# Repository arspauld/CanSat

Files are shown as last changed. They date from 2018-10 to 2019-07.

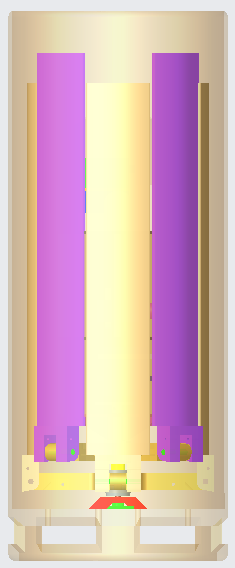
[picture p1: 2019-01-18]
mechanical/Screenshots from main folder/in container.PNG

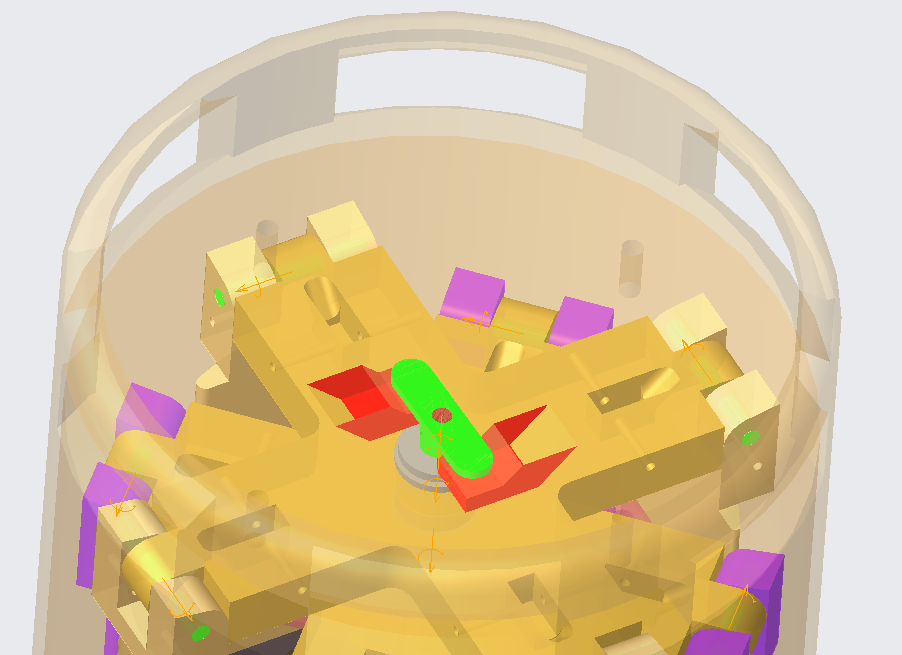
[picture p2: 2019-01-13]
mechanical/Screenshots from main folder/Release Mechanism Latched_2.PNG

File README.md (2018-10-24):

## Welcome to GitHub Pages

You can use the [editor on GitHub](https://github.com/arspauld/CanSat/edit/master/README.md) to maintain and preview the content for your website in Markdown files.

Whenever you commit to this repository, GitHub Pages will run [Jekyll](https://jekyllrb.com/) to rebuild the pages in your site, from the content in your Markdown files.

### Markdown

Markdown is a lightweight and easy-to-use syntax for styling your writing. It includes conventions for

```markdown
Syntax highlighted code block

# Header 1
## Header 2
### Header 3

- Bulleted
- List

1. Numbered
2. List

**Bold** and _Italic_ and `Code` text

[Link](url) and ![Image](src)
```

For more details see [GitHub Flavored Markdown](https://guides.github.com/features/mastering-markdown/).

### Jekyll Themes

Your Pages site will use the layout and styles from the Jekyll theme you have selected in your [repository settings](https://github.com/arspauld/CanSat/settings). The name of this theme is saved in the Jekyll `_config.yml` configuration file.

### Support or Contact

Having trouble with Pages? Check out our [documentation](https://help.github.com/categories/github-pages-basics/) or [contact support](https://github.com/contact) and we’ll help you sort it out.

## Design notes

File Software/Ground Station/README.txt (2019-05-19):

This is the folder for the files used on the ground station.
This will be done in Python programming

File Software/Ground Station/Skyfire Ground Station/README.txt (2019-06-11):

Skyfire Ground Station Setup:
	1. Insert XBee module into USB drive on laptop
	2. Open device manager and search for the port the XBee module is recognized as
	3. Open main.py and change the port in line <line #> to the exact name the XBee is recognized as in the device manager
	4. Open terminal
	5. Navigate to the Ground Station folder
	6. Run the file by typing "python main.py"

****There is a "frozen" instance of main.py that runs like an executable if the XBee is recognized as the same port as dictated by the program

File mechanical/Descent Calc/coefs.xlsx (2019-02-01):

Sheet: Cl and Cd
Alpha | Cl | Cd
-10 | -0.8195 | 0.07577
-9.75 | -0.8355 | 0.07025
-9.5 | -0.8519 | 0.06488
-9.25 | -0.8654 | 0.05977
-9 | -0.8743 | 0.055
-8.75 | -0.8723 | 0.05095
-8.5 | -0.8537 | 0.04867
-8.25 | -0.8499 | 0.04511
-8 | -0.8371 | 0.04218
-7.75 | -0.8225 | 0.03983
-7.5 | -0.8044 | 0.03756
-7.25 | -0.7876 | 0.0354
-7 | -0.7691 | 0.0335
-6.75 | -0.7491 | 0.03186
-6.5 | -0.7296 | 0.03038
-6.25 | -0.7105 | 0.02892
-6 | -0.6919 | 0.02765
-5.75 | -0.673 | 0.02658
-5.5 | -0.6548 | 0.02564
-5.25 | -0.6369 | 0.02482
-5 | -0.6195 | 0.02413
-4.75 | -0.6002 | 0.02367
-4.5 | -0.5816 | 0.02327
-4.25 | -0.5628 | 0.023
-4 | -0.5431 | 0.02285
-3.75 | -0.5227 | 0.02282
-3.5 | -0.503 | 0.02279
-3.25 | -0.4793 | 0.02298
-3 | -0.4493 | 0.02334
-2.75 | -0.4085 | 0.02382
-2.5 | -0.35 | 0.02437
-2.25 | -0.2694 | 0.02476
-2 | -0.1829 | 0.02464
-1.75 | -0.1037 | 0.02407
-1.5 | -0.0223 | 0.02312
-1.25 | 0.0255 | 0.0222
-1 | 0.0285 | 0.02168
-0.75 | 0.0275 | 0.02128
-0.5 | 0.0225 | 0.021
-0.25 | 0.0128 | 0.02083
0 | 0 | 0.02078
0.25 | -0.0128 | 0.02083
0.5 | -0.0225 | 0.02099
0.75 | -0.0275 | 0.02128
1 | -0.0285 | 0.02168
1.25 | -0.0255 | 0.02219
1.5 | 0.0223 | 0.02311
1.75 | 0.1036 | 0.02406
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

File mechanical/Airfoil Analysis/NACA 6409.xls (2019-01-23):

NACA 6409
1.00000 0.00094 | 0
0.99280 0.00313 | 0
0.97989 0.00699 | 0
0.96352 0.01177 | 0
0.94455 0.01717 | 0
0.92350 0.02296 | 0
0.90075 0.02900 | 0
0.87658 0.03516 | 0
0.85123 0.04135 | 0
0.82489 0.04749 | 0
0.79774 0.05350 | 0
0.76991 0.05932 | 0
0.74154 0.06492 | 0
0.71275 0.07024 | 0
0.68365 0.07525 | 0
0.65434 0.07992 | 0
0.62492 0.08422 | 0
0.59547 0.08814 | 0
0.56607 0.09165 | 0
0.53680 0.09474 | 0
0.50774 0.09740 | 0
0.47895 0.09963 | 0
0.45050 0.10141 | 0
0.42246 0.10275 | 0
0.39488 0.10365 | 0
0.36782 0.10391 | 0
0.34135 0.10345 | 0
0.31551 0.10230 | 0
0.29035 0.10049 | 0
0.26594 0.09807 | 0
0.24231 0.09508 | 0
0.21951 0.09156 | 0
0.19760 0.08756 | 0
0.17661 0.08315 | 0
0.15660 0.07836 | 0
0.13760 0.07326 | 0
0.11965 0.06790 | 0
0.10280 0.06235 | 0
0.08709 0.05666 | 0
0.07256 0.05088 | 0
0.05924 0.04509 | 0
0.04717 0.03932 | 0
0.03639 0.03364 | 0
0.02694 0.02810 | 0
0.01885 0.02274 | 0
0.01215 0.01760 | 0
0.00688 0.01273 | 0
0.00308 0.00816 | 0
0.00078 0.00391 | 0
0.00000 0.00000 | 0
0.00078 -0.00344 | 0
0.00308 -0.00632 | 0
0.00688 -0.00864 | 0
0.01215 -0.01043 | 0
0.01885 -0.01170 | 0
0.02694 -0.01248 | 0
0.03639 -0.01280 | 0
0.04717 -0.01269 | 0
0.05924 -0.01217 | 0
0.07256 -0.01130 | 0
0.08709 -0.01009 | 0
0.10280 -0.00859 | 0
0.11965 -0.00685 | 0
0.13760 -0.00490 | 0
0.15660 -0.00279 | 0
0.17661 -0.00057 | 0
0.19760 0.00171 | 0
0.21951 0.00401 | 0
0.24231 0.00627 | 0
0.26594 0.00845 | 0
0.29035 0.01049 | 0
0.31551 0.01235 | 0
0.34135 0.01397 | 0
0.36782 0.01531 | 0
0.39488 0.01633 | 0
0.42246 0.01708 | 0
0.45050 0.01774 | 0
0.47895 0.01830 | 0
0.50774 0.01873 | 0
0.53680 0.01902 | 0
0.56607 0.01916 | 0
0.59547 0.01913 | 0
0.62492 0.01892 | 0
0.65434 0.01852 | 0
0.68365 0.01793 | 0
0.71275 0.01716 | 0
0.74154 0.01620 | 0
0.76991 0.01507 | 0
0.79774 0.01377 | 0
0.82489 0.01234 | 0
0.85123 0.01078 | 0
0.87658 0.00913 | 0
0.90075 0.00742 | 0
0.92350 0.00569 | 0
0.94455 0.00399 | 0
0.96352 0.00238 | 0
0.97989 0.00092 | 0
0.99280 -0.00027 | 0
1.00000 -0.00094 | 0

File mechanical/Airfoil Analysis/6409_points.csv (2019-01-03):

x | y | z
1 | 0.00094 | 0
0.9928 | 0.00313 | 0
0.97989 | 0.00699 | 0
0.96352 | 0.01177 | 0
0.94455 | 0.01717 | 0
0.9235 | 0.02296 | 0
0.90075 | 0.029 | 0
0.87658 | 0.03516 | 0
0.85123 | 0.04135 | 0
0.82489 | 0.04749 | 0
0.79774 | 0.0535 | 0
0.76991 | 0.05932 | 0
0.74154 | 0.06492 | 0
0.71275 | 0.07024 | 0
0.68365 | 0.07525 | 0
0.65434 | 0.07992 | 0
0.62492 | 0.08422 | 0
0.59547 | 0.08814 | 0
0.56607 | 0.09165 | 0
0.5368 | 0.09474 | 0
0.50774 | 0.0974 | 0
0.47895 | 0.09963 | 0
0.4505 | 0.10141 | 0
0.42246 | 0.10275 | 0
0.39488 | 0.10365 | 0
0.36782 | 0.10391 | 0
0.34135 | 0.10345 | 0
0.31551 | 0.1023 | 0
0.29035 | 0.10049 | 0
0.26594 | 0.09807 | 0
0.24231 | 0.09508 | 0
0.21951 | 0.09156 | 0
0.1976 | 0.08756 | 0
0.17661 | 0.08315 | 0
0.1566 | 0.07836 | 0
0.1376 | 0.07326 | 0
0.11965 | 0.0679 | 0
0.1028 | 0.06235 | 0
0.08709 | 0.05666 | 0
0.07256 | 0.05088 | 0
0.05924 | 0.04509 | 0
0.04717 | 0.03932 | 0
0.03639 | 0.03364 | 0
0.02694 | 0.0281 | 0
0.01885 | 0.02274 | 0
0.01215 | 0.0176 | 0
0.00688 | 0.01273 | 0
0.00308 | 0.00816 | 0
0.00078 | 0.00391 | 0
0 | 0 | 0
0.00078 | -0.00344 | 0
0.00308 | -0.00632 | 0
0.00688 | -0.00864 | 0
0.01215 | -0.01043 | 0
0.01885 | -0.0117 | 0
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

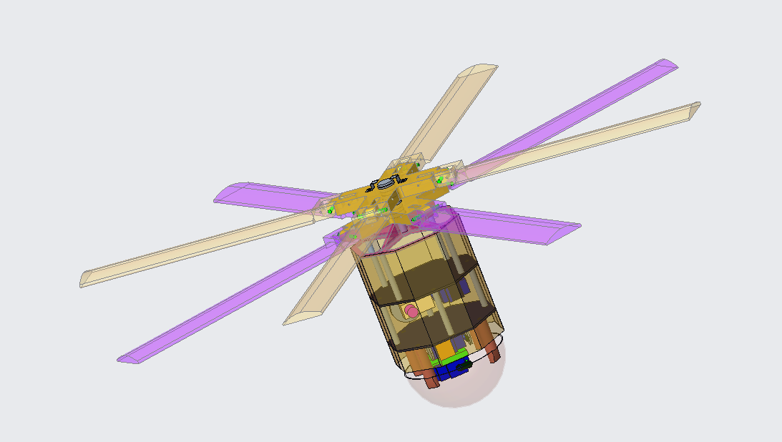
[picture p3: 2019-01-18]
mechanical/Screenshots from main folder/iso view.PNG

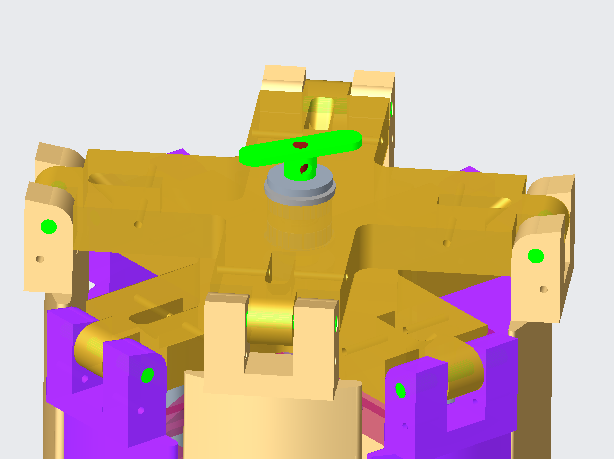
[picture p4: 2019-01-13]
mechanical/Screenshots from main folder/Top Release Mechanism.PNG

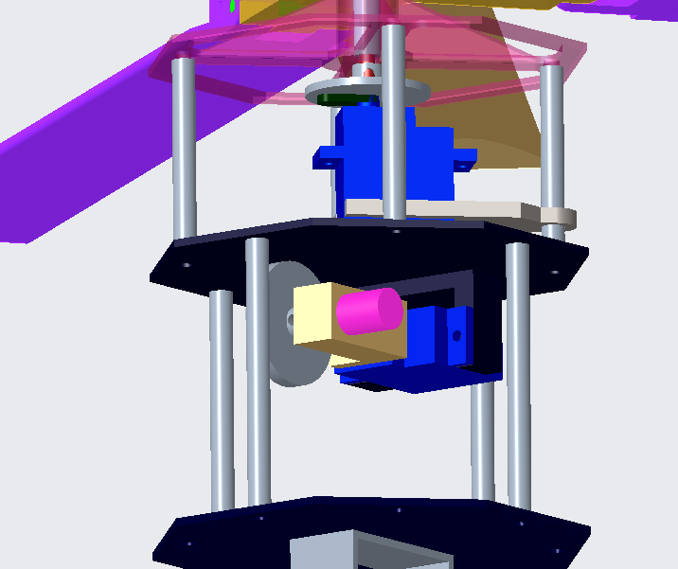
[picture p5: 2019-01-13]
mechanical/Screenshots from main folder/Control Moment Gyro 4.PNG

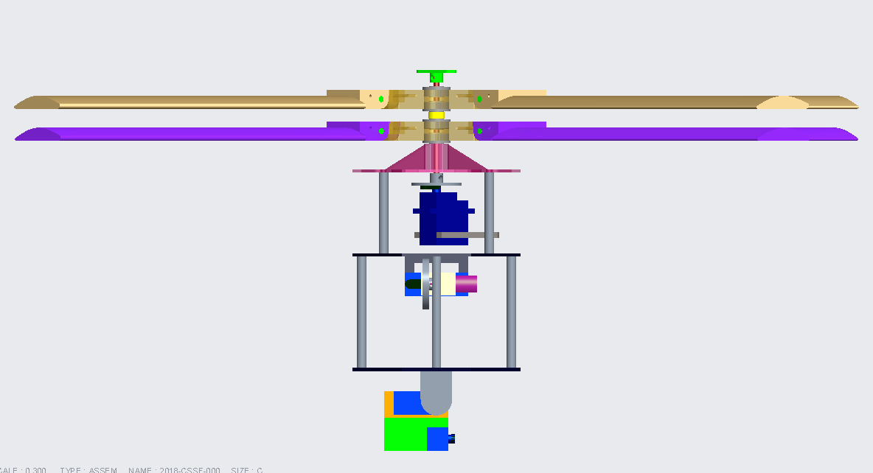
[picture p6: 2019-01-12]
mechanical/Screenshots from main folder/Full deployed Drawing.PNG

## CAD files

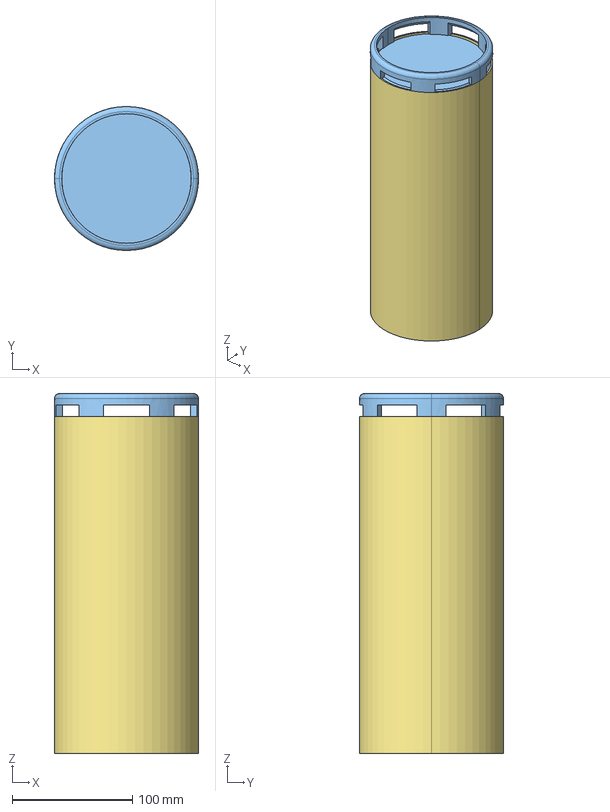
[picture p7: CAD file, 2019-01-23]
mechanical/2018-cssf-000_asm.stp
120.0 x 120.0 x 300.0 mm
2018-CSSF-101
2018-CSSF-102 x 4
2018-CSSF-103
2018-CSSF-106 x 4
2018-CSSF-105
MICRO_SERVO x 4
SERVO_ARM x 3
2018-CSSF-502
GYRO_MOTOR
2018-CSSF-501
2018-CSSF-201
2018-CSSF-202
2018-CSSF-203
2018-CSSF-301
57155K337_STAINLESS_STEEL_BALL_ x 6
2018-CSSF-303_TOP
2018-CSSF-302
2018-CSSF-303
ROTOR1_WING x 4
2018-CSSF-306 x 12
ROTOR2_WING x 4
2018-CSSF-301B
2018-CSSF-307B
2018-CSSF-305B x 4
2018-CSSF-307 x 2
CONTAINER
CAMERA_DOME
6409_NACA_ROTOR
DOME_OFFSET x 4
CANSAT_SHELL x 2
CONTAINER_SLEEVE_1
SERVO_ARM_FULL_LENGTH
RELEASE_CATCH x 2
PAYLOAD_DOWEL x 2

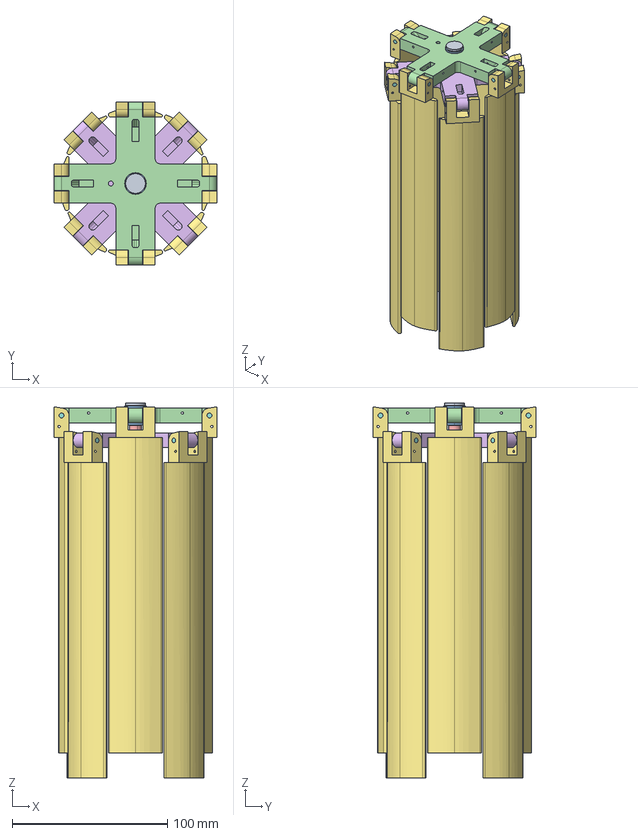
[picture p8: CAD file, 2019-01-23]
mechanical/SolidEdge/Original Creo Parts/2018-cssf-300_asm.stp
104.8 x 104.8 x 241.5 mm
2018-CSSF-301
57155K337_STAINLESS_STEEL_BALL_ x 4
2018-CSSF-303_TOP
2018-CSSF-302
2018-CSSF-303
ROTOR1_WING x 4
2018-CSSF-306 x 8
ROTOR2_WING x 4

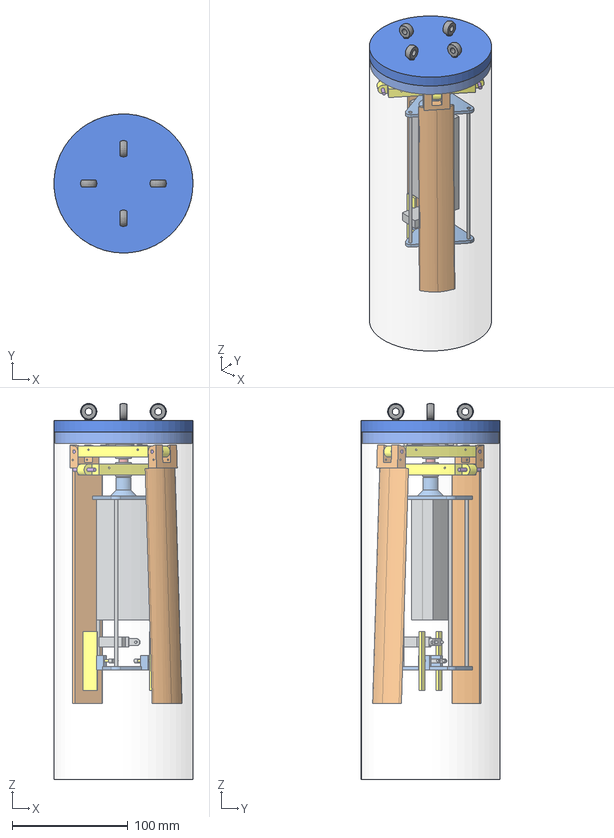
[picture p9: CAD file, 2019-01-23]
mechanical/SolidEdge/Container Parts/Container Assembly_v3.stp
120.0 x 120.0 x 324.5 mm
Container Top
Container Shell
Wooden Dowel M3 x 2
M6 EyeBolt x 4
m3_all_thread x 3
hardware_plate
FIN_LEVER x 2
BALL_PIN x 4
FIN x 2
NANO_SERVO_HS-40
SERVO_ARM
HARDWARE_BOTTOM_PLATE_V2
2018-CSSF-301
57155K337_STAINLESS_STEEL_BALL_ x 4
2018-CSSF-303_TOP
2018-CSSF-302
2018-CSSF-303
ROTOR1_WING x 2
ROTOR2_WING x 2
2018-CSSF-306 x 4
Lip1 x 2
3.2mm screw x 3
PCB_CASE_BACK
PCB
PCB_CASE_FRONT

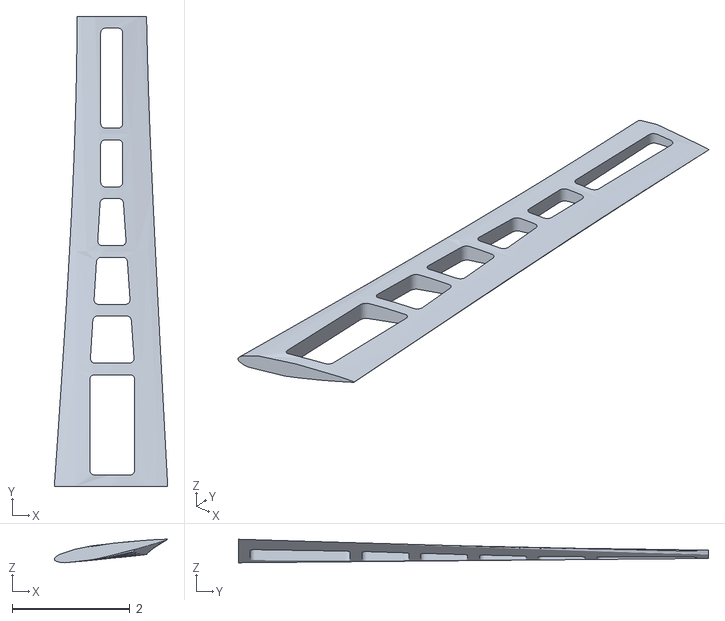
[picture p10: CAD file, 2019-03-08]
mechanical/AIRFOIL X-SECTIONS/20cm_0012_rotor_lh.stl
1.93 x 7.99 x 0.401

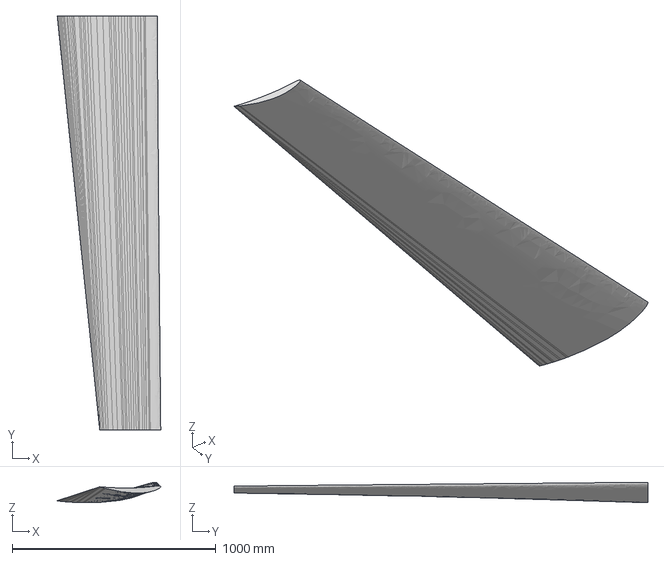
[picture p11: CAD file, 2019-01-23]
mechanical/Naca/6409_blade.step
507.9 x 2030.0 x 100.4 mm

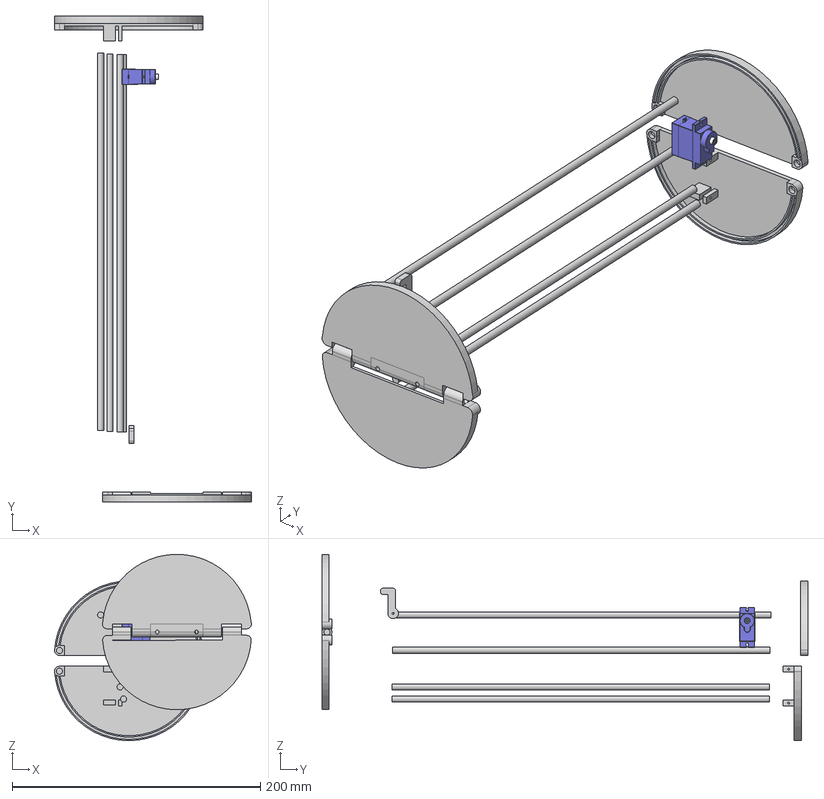
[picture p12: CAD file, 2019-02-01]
mechanical/SolidEdge/2nd Container Design/Container 2 parts.step
158.7 x 391.4 x 150.1 mm
Outer Top
Top 1
Rod x 4
Bottom empty half
Bottom servo half
servo

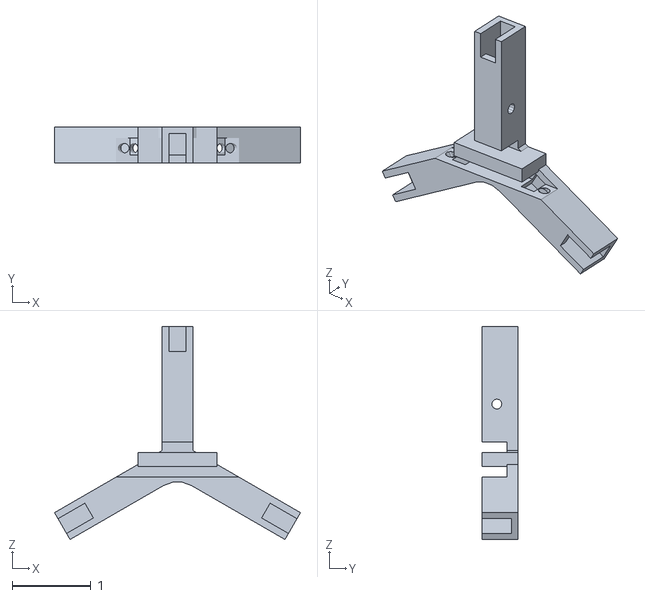
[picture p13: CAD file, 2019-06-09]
mechanical/SolidEdge/3 Blade/LANDING_GEAR_MOUNT.stl
3.12 x 0.453 x 2.70

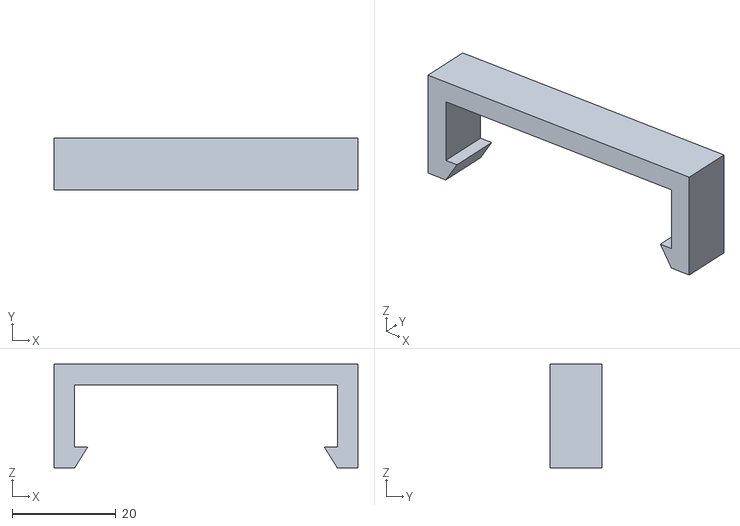
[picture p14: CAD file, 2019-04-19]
mechanical/SolidEdge/Battery Parts/BATTERY_LOCK.stl
58.7 x 10.0 x 20.0

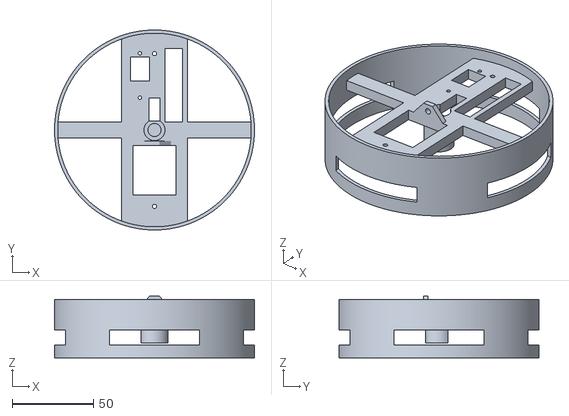
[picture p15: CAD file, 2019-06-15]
mechanical/SolidEdge/Container Parts/Container Top V4.stl
123.0 x 123.0 x 38.0

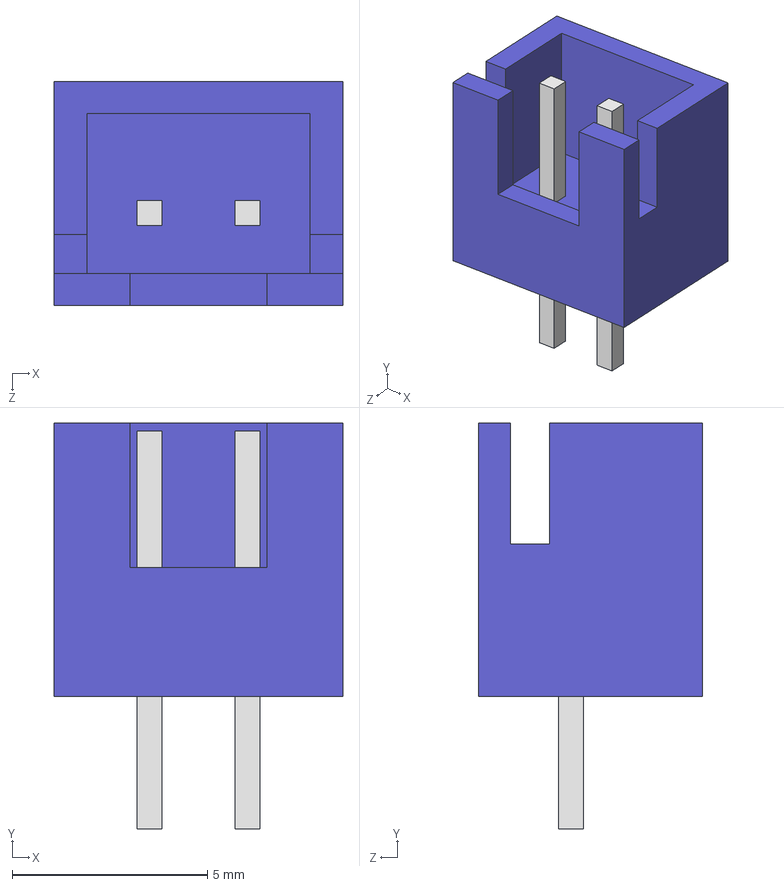
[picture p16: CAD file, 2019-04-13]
mechanical/SolidEdge/Electronics Parts/B2B-XH-A.IGS
7.40 x 10.4 x 5.75 mm

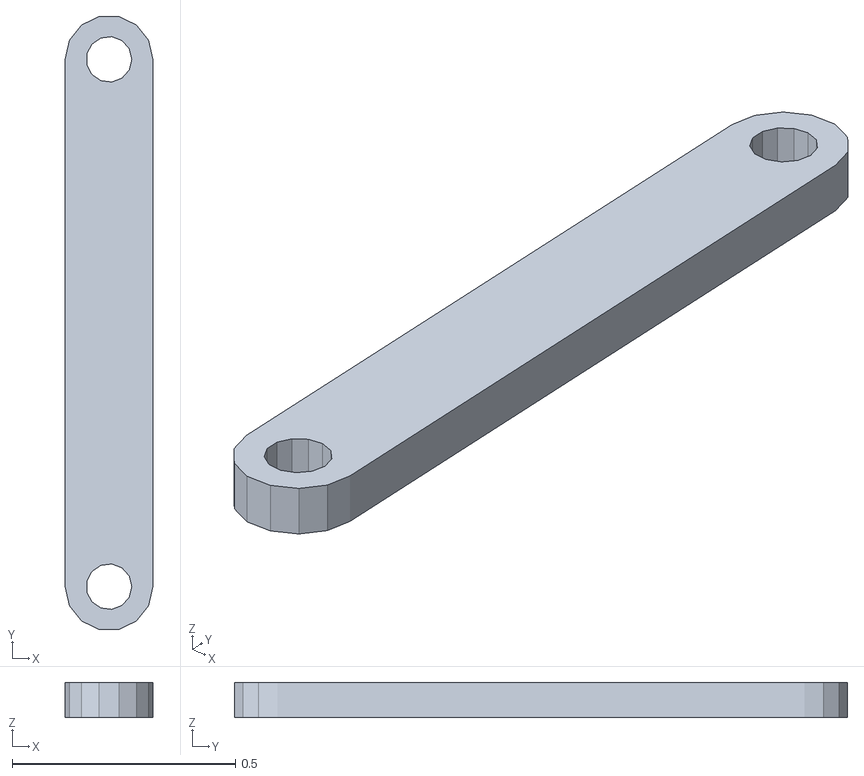
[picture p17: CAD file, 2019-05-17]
mechanical/SolidEdge/Fin Designs/control_arm.stl
0.197 x 1.37 x 0.0787

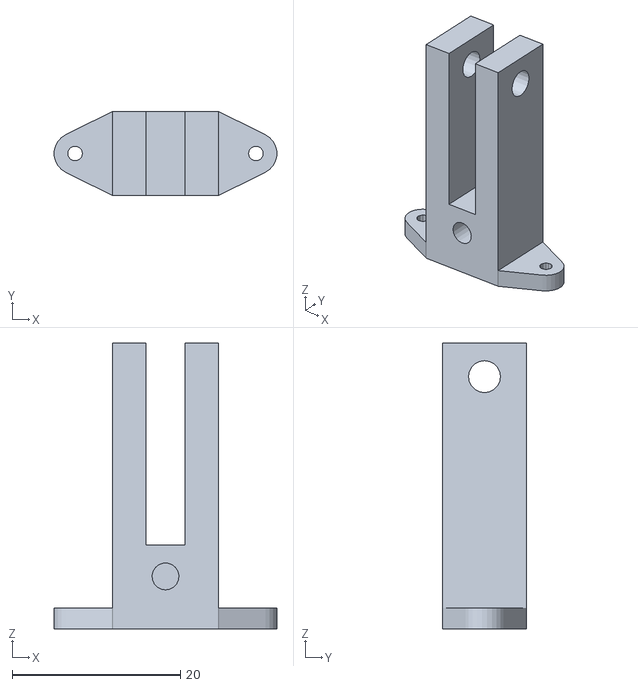
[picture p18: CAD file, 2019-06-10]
mechanical/SolidEdge/Fin Designs/Fin Redesign/FinR_connector_V1.stl
26.5 x 10.0 x 34.0

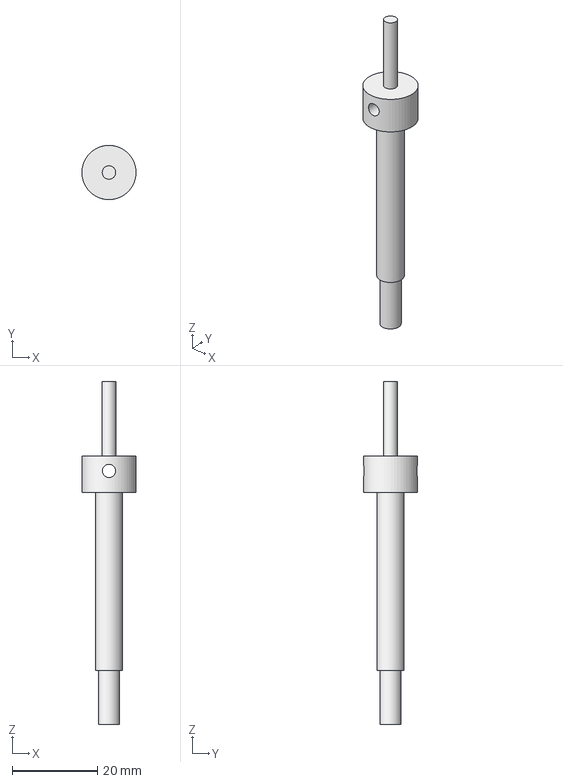
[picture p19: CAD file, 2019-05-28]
mechanical/SolidEdge/Original Creo Parts/2018-CSSF-301.stp
12.7 x 12.7 x 80.3 mm

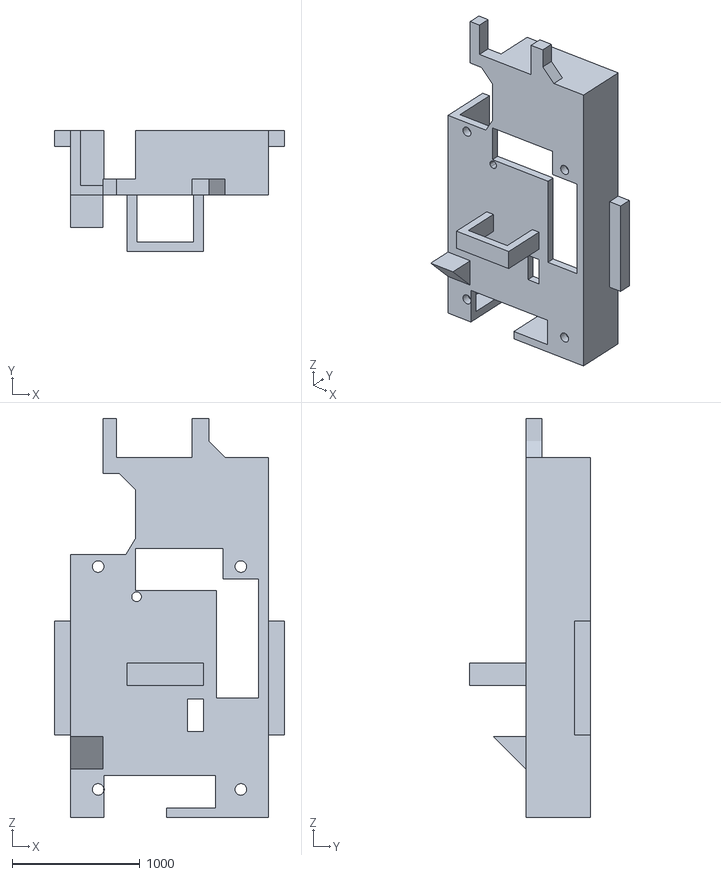
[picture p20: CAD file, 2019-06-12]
mechanical/SolidEdge/PCB Cases/PCB_CASE_V5_FRONT.stl
1803.4 x 950.6 x 3124.2

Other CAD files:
mechanical/SolidEdge/RELEASE_ARM.stl
mechanical/SolidEdge/Rotor Parts/hub_adapter_signboard v1.stl
mechanical/SolidEdge/U-Frame/U-frame_top_draft_model.stp
mechanical/AIRFOIL X-SECTIONS/20cm_0012_rotor.stl
mechanical/AIRFOIL X-SECTIONS/20cm_0012_rotor_xsect_1.stl
mechanical/AIRFOIL X-SECTIONS/20cm_0012_rotor_xsect_1_mirror.stl
mechanical/AIRFOIL X-SECTIONS/20cm_0012_rotor_xsect_2.stl
mechanical/AIRFOIL X-SECTIONS/20cm_0012_rotor_xsect_2_mirror.stl
mechanical/AIRFOIL X-SECTIONS/20cm_0012_rotor_xsect_3.stl
mechanical/AIRFOIL X-SECTIONS/20cm_0012_rotor_xsect_3_mirror.stl
mechanical/AIRFOIL X-SECTIONS/20cm_0012_rotor_xsect_4.stl
mechanical/AIRFOIL X-SECTIONS/20cm_0012_rotor_xsect_4_mirror.stl
mechanical/AIRFOIL X-SECTIONS/20cm_0012_rotor_xsect_5.stl
mechanical/AIRFOIL X-SECTIONS/20cm_0012_rotor_xsect_5_mirror.stl
mechanical/AIRFOIL X-SECTIONS/20cm_0012_rotor_xsect_6.stl
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

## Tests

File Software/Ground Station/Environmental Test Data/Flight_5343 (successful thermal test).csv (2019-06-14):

Team ID | Mission Time | Packet Count | Altitude | Pressure | Temperature | Voltage | GPS Time | GPS Latitude | GPS Longitude | GPS Altitude | GPS Sats | Pitch | Roll | Blade Spin Rate | Flight State | Bonus Direction
5343 | 1 | 1 | 0.1 | 96969 | 47.8 | 5.6 | 16:12:16 | 0 | 0 | 0 | 0 | 0 | 0 | 0 | 0 | 154
5343 | 2 | 2 | 0.2 | 96970 | 47.9 | 5.6 | 16:12:17 | 0 | 0 | 0 | 0 | 0 | 0 | 0 | 0 | 154
5343 | 3 | 3 | 0.1 | 96969 | 47.8 | 5.6 | 16:12:18 | 0 | 0 | 0 | 0 | 0 | 0 | 0 | 0 | 154
5343 | 4 | 4 | 0.2 | 96970 | 47.8 | 5.6 | 16:12:19 | 0 | 0 | 0 | 0 | 0 | 0 | 0 | 0 | 154
5343 | 5 | 5 | 0.3 | 96971 | 47.8 | 5.6 | 16:12:20 | 0 | 0 | 0 | 0 | 0 | 0 | 0 | 0 | 154
5343 | 6 | 6 | 0.5 | 96973 | 47.8 | 5.6 | 16:12:21 | 0 | 0 | 0 | 0 | 0 | 0 | 0 | 0 | 154
5343 | 7 | 7 | 0.5 | 96973 | 47.8 | 5.6 | 16:12:22 | 0 | 0 | 0 | 0 | 0 | 0 | 0 | 0 | 154
5343 | 8 | 8 | 0.3 | 96971 | 47.8 | 5.6 | 16:12:23 | 0 | 0 | 0 | 0 | 0 | 0 | 0 | 0 | 154
5343 | 9 | 9 | 0.5 | 96973 | 47.9 | 5.5 | 16:12:24 | 0 | 0 | 0 | 0 | 0 | 0 | 0 | 0 | 154
5343 | 10 | 10 | 0.7 | 96975 | 48 | 5.6 | 16:12:25 | 0 | 0 | 0 | 0 | 0 | 0 | 0 | 0 | 154
5343 | 11 | 11 | 0.6 | 96974 | 48.1 | 5.6 | 16:12:26 | 0 | 0 | 0 | 0 | 0 | 0 | 0 | 0 | 154
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

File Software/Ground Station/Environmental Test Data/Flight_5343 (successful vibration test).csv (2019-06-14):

Team ID | Mission Time | Packet Count | Altitude | Pressure | Temperature | Voltage | GPS Time | GPS Latitude | GPS Longitude | GPS Altitude | GPS Sats | Pitch | Roll | Blade Spin Rate | Flight State | Bonus Direction
5343 | 351 | 351 | -1.7 | 97111 | 32.5 | 5.4 | 04:47:06 | 0.0 | 0.0 | 0.0 | 0 | -6 | -5 | 0 | 0 | 35
5343 | 352 | 352 | -1.8 | 97112 | 32.5 | 5.4 | 04:47:07 | 0.0 | 0.0 | 0.0 | 0 | 1 | 2 | 0 | 0 | 35
5343 | 353 | 353 | -1.7 | 97111 | 32.5 | 5.5 | 04:47:08 | 0.0 | 0.0 | 0.0 | 0 | 1 | 2 | 0 | 0 | 35
5343 | 354 | 354 | -1.7 | 97111 | 32.5 | 5.4 | 04:47:09 | 0.0 | 0.0 | 0.0 | 0 | 1 | 2 | 0 | 0 | 35
5343 | 355 | 355 | -1.7 | 97111 | 32.5 | 5.4 | 04:47:10 | 0.0 | 0.0 | 0.0 | 0 | 1 | 2 | 0 | 0 | 35
5343 | 1 | 1 | 0.0 | 97112 | 32.5 | 5.4 | 04:47:15 | 0.0 | 0.0 | 0.0 | 0 | 0 | -7 | 0 | 0 | 35
5343 | 2 | 2 | 0.1 | 97114 | 32.5 | 5.4 | 04:47:15 | 0.0 | 0.0 | 0.0 | 0 | 0 | 0 | 0 | 0 | 35
5343 | 3 | 3 | 0.0 | 97113 | 32.4 | 4.5 | 04:47:16 | 0.0 | 0.0 | 0.0 | 0 | 0 | 0 | 0 | 0 | 35
5343 | 4 | 4 | 0.1 | 97113 | 32.5 | 5.4 | 04:47:17 | 0.0 | 0.0 | 0.0 | 0 | 0 | 0 | 0 | 0 | 35
5343 | 5 | 5 | 0.1 | 97113 | 32.4 | 5.4 | 04:47:18 | 0.0 | 0.0 | 0.0 | 0 | 0 | 0 | 0 | 0 | 35
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

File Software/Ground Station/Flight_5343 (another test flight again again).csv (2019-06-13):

Team ID | Mission Time | Packet Count | Altitude | Pressure | Temperature | Voltage | GPS Time | GPS Latitude | GPS Longitude | GPS Altitude | GPS Sats | Pitch | Roll | Blade Spin Rate | Flight State | Bonus Direction
5343 | 1 | 1 | 0 | 98635 | 23.5 | 2.7 | 00:00:00 | 0.0 | 0.0 | 0.0 | 0 | 0 | 0 | 30 | 0 | 0
5343 | 2 | 2 | 0 | 98637 | 23.4 | 2.6 | 00:00:00 | 0.0 | 0.0 | 0.0 | 0 | 0 | 0 | 15 | 0 | 0
5343 | 3 | 3 | 0 | 98636 | 23.0 | 2.6 | 00:00:00 | 0.0 | 0.0 | 0.0 | 0 | 0 | 0 | 7 | 0 | 0
5343 | 4 | 4 | 0 | 98637 | 23.0 | 2.6 | 00:00:00 | 0.0 | 0.0 | 0.0 | 0 | 0 | 0 | 3 | 0 | 0
5343 | 5 | 5 | 0 | 98635 | 22.9 | 2.6 | 00:00:00 | 0.0 | 0.0 | 0.0 | 0 | 0 | 0 | 1 | 0 | 0
5343 | 6 | 6 | 0 | 98635 | 25.2 | 2.8 | 00:00:00 | 0.0 | 0.0 | 0.0 | 0 | 0 | 0 | 2580 | 0 | 0
5343 | 7 | 7 | 0 | 98634 | 25.2 | 2.8 | 00:00:00 | 0.0 | 0.0 | 0.0 | 0 | 0 | 0 | 1350 | 0 | 0
5343 | 8 | 8 | 0 | 98638 | 25.5 | 2.8 | 00:00:00 | 0.0 | 0.0 | 0.0 | 0 | 0 | 0 | 945 | 0 | 0
5343 | 9 | 9 | 0 | 98636 | 25.3 | 2.8 | 00:00:00 | 0.0 | 0.0 | 0.0 | 0 | 0 | 0 | 682 | 0 | 0
5343 | 10 | 10 | 0 | 98637 | 25.4 | 2.8 | 00:00:00 | 0.0 | 0.0 | 0.0 | 0 | 0 | 0 | 341 | 0 | 0
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

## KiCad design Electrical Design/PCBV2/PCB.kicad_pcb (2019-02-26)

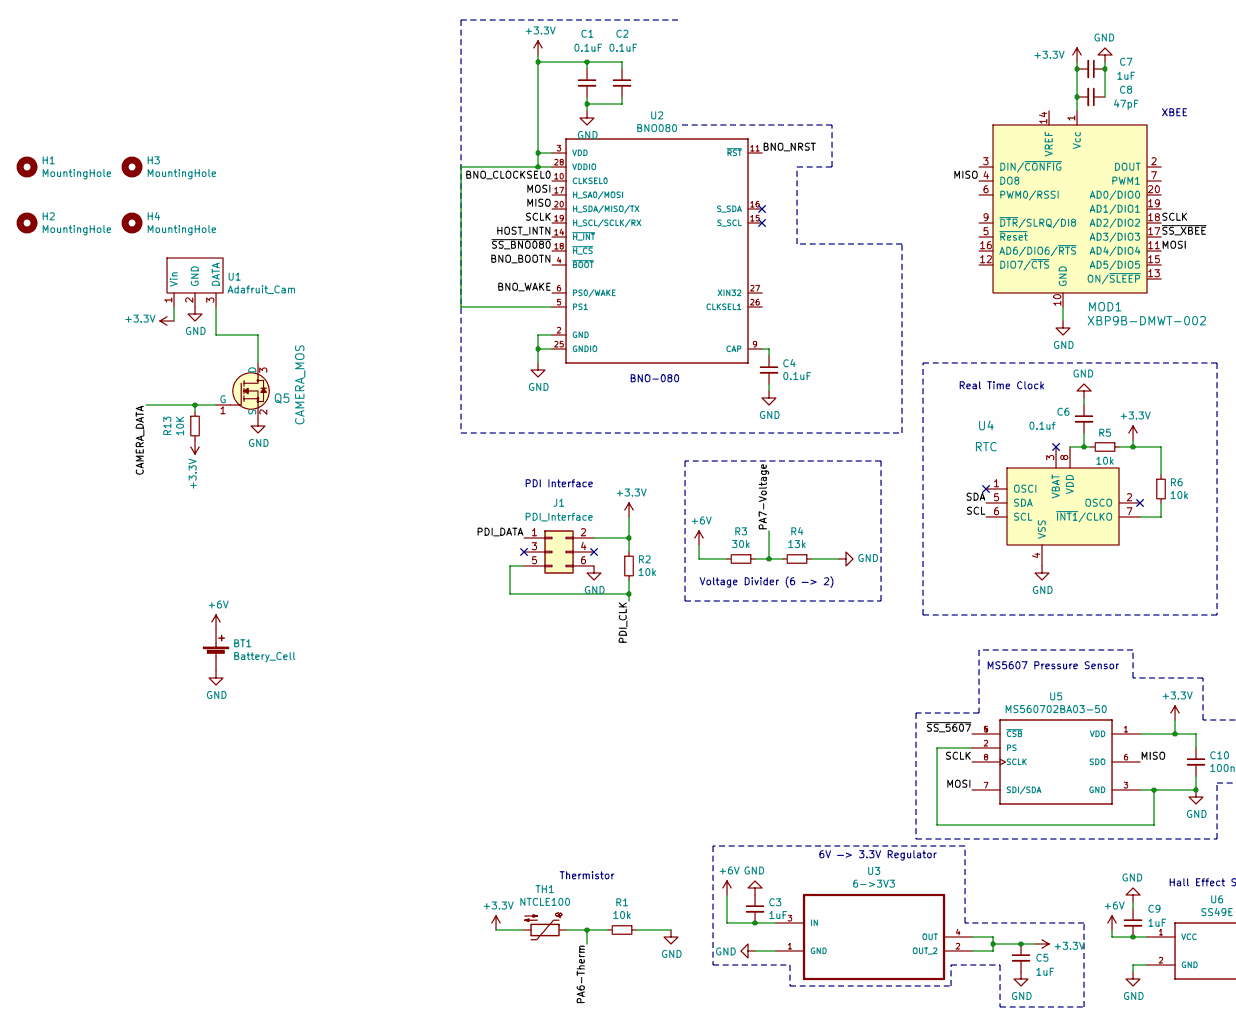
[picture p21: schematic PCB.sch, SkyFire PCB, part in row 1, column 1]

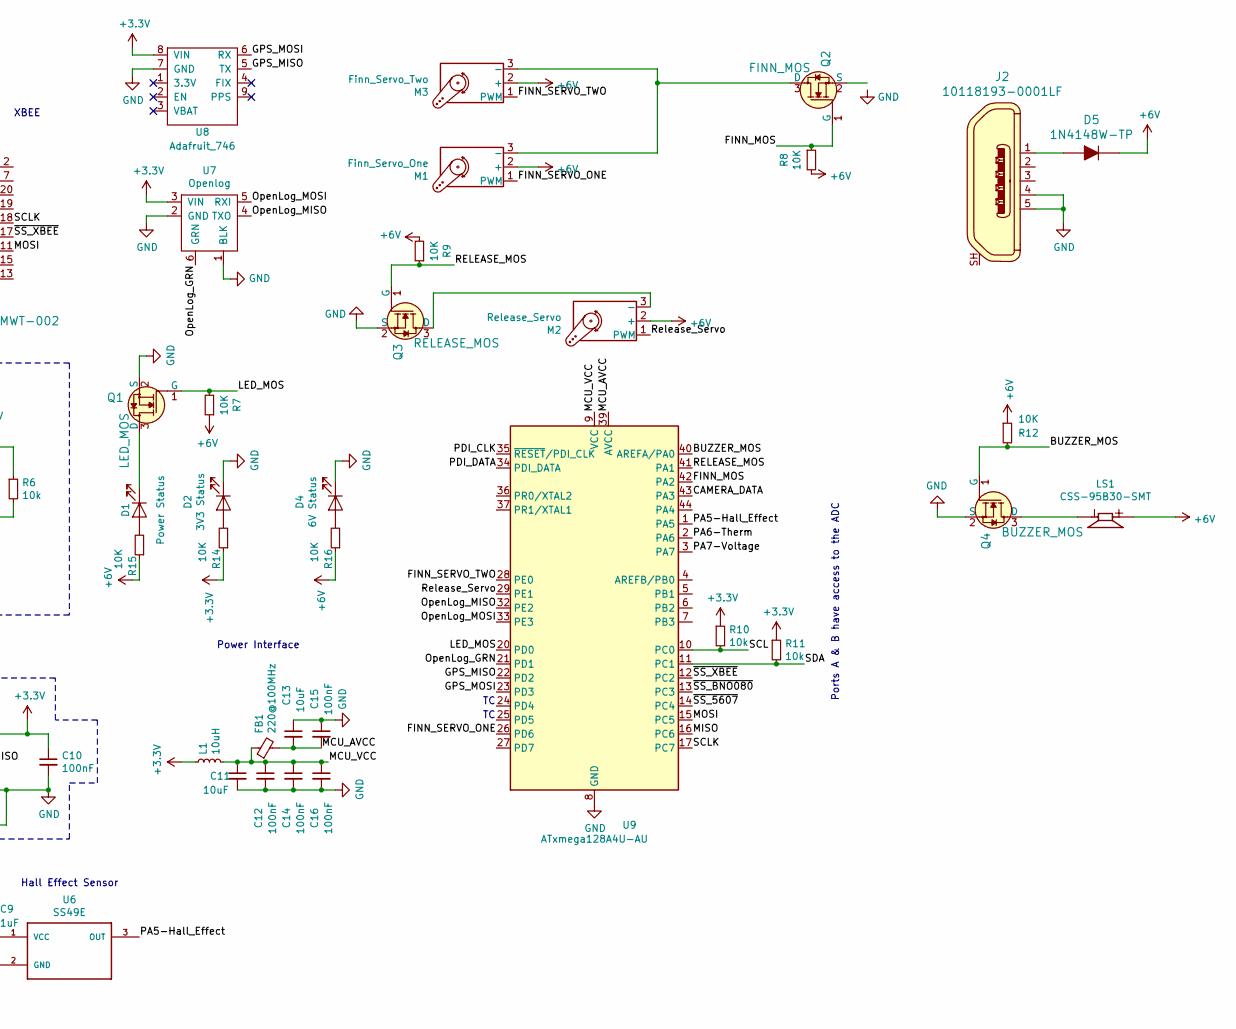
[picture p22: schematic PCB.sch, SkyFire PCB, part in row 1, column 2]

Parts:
BT1: Battery_Cell; MOLEX-1X2_LOCK
C1, C2, C4: 0.1uF; C_0805_2012Metric_Pad1.15x1.40mm_HandSolder
C3, C5, C7, C9: 1uF; C_0805_2012Metric_Pad1.15x1.40mm_HandSolder
C6: 0.1uf; C_0805_2012Metric_Pad1.15x1.40mm_HandSolder
C8: 47pF; C_0805_2012Metric_Pad1.15x1.40mm_HandSolder
C10, C12, C14, C15, C16: 100nF; C_0805_2012Metric_Pad1.15x1.40mm_HandSolder
C11, C13: 10uF; C_0805_2012Metric_Pad1.15x1.40mm_HandSolder
D1: Power Status; LED_0603_1608Metric_Pad1.05x0.95mm_HandSolder
D2: 3V3 Status; LED_0603_1608Metric_Pad1.05x0.95mm_HandSolder
D4: 6V Status; LED_0603_1608Metric_Pad1.05x0.95mm_HandSolder
D5: 1N4148W-TP; SOD-123; MPN 1N4148W-TP; Digi-Key_PN 1N4148WTPMSCT-ND
FB1: 220@100MHz; L_0805_2012Metric_Pad1.15x1.40mm_HandSolder
H1, H2, H3, H4: MountingHole; MountingHole_3.2mm_M3
J1: PDI_Interface; 2X3
J2: 10118193-0001LF; USB_Micro_B_Female_10118193-0001LF; MPN 10118193-0001LF; Digi-Key_PN 609-4616-1-ND
L1: 10uH; L_0805_2012Metric_Pad1.15x1.40mm_HandSolder
LS1: CSS-95B30-SMT; CUI_CSS-95B30-SMT
M1: Finn_Servo_One; MOLEX-1X3_LOCK
M2: Release_Servo; MOLEX-1X3_LOCK
M3: Finn_Servo_Two; MOLEX-1X3_LOCK
MOD1: XBP9B-DMWT-002; XBEE_PRO-20_THT; MPN XBP9B-DMWT-002; Digi-Key_PN 602-1301-ND
Q1: LED_MOS; SOT-23-3; MPN 2N7002K-T1-E3; Digi-Key_PN 2N7002K-T1-E3CT-ND
Q2: FINN_MOS; SOT-23-3; MPN 2N7002K-T1-E3; Digi-Key_PN 2N7002K-T1-E3CT-ND
Q3: RELEASE_MOS; SOT-23-3; MPN 2N7002K-T1-E3; Digi-Key_PN 2N7002K-T1-E3CT-ND
Q4: BUZZER_MOS; SOT-23-3; MPN 2N7002K-T1-E3; Digi-Key_PN 2N7002K-T1-E3CT-ND
Q5: CAMERA_MOS; SOT-23-3; MPN 2N7002K-T1-E3; Digi-Key_PN 2N7002K-T1-E3CT-ND
R1, R2, R5, R6, R10, R11: 10k; R_0805_2012Metric_Pad1.15x1.40mm_HandSolder
R3: 30k; R_0805_2012Metric_Pad1.15x1.40mm_HandSolder
R4: 13k; R_0805_2012Metric_Pad1.15x1.40mm_HandSolder
R7, R8, R9, R12, R13, R14, R15, R16: 10K; R_0805_2012Metric_Pad1.15x1.40mm_HandSolder
TH1: NTCLE100; CP_Radial_D4.0mm_P1.50mm
U1: Adafruit_Cam; MOLEX-1X3_LOCK
U2: BNO080; LGA-28
U3: 6->3V3; SOT230P700X180-4N
U4: RTC; SOIC-8_W3.9mm; MPN PCF8523T/1,118; Digi-Key_PN 568-5306-1-ND
U5: MS560702BA03-50; SON125P300X500X100-8N
U6: SS49E; MOLEX-1X3_LOCK
U7: Openlog; 1X06
U8: Adafruit_746; 1X09
U9: ATxmega128A4U-AU; TQFP-44_10x10mm_P0.8mm

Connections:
+3V3: C1.1, C2.1, C5.1, C7.2, C8.2, C10.1, J1.2, L1.1, MOD1.1 (Vcc), R2.1, R5.1, R6.1, R10.1, R11.1, R13.2, R14.1, TH1.2, U1.1 (Vin), U2.3 (VDD), U2.5 (PS1), U2.28 (VDDIO), U3.2 (OUT_2), U3.4 (OUT), U5.1 (VDD), U7.3 (VIN), U8.8 (VIN)
+6V: BT1.1 (+), C3.2, C9.2, D5.K, LS1.P, M1.2 (+), M2.2 (+), M3.2 (+), R3.2, R7.1, R8.2, R9.2, R12.1, R15.1, R16.1, U3.3 (IN), U6.1 (VCC)
/BNO_BOOTN: U2.4 (~BOOT~)
/BNO_CLOCKSEL0: U2.10 (CLKSEL0)
/BNO_NRST: U2.11 (~RST~)
/BNO_WAKE: U2.6 (PS0/WAKE)
/BUZZER_MOS: Q4.1 (G), R12.2, U9.40 (AREFA/PA0)
/CAMERA_DATA: Q5.1 (G), R13.1, U9.43 (PA3)
/FINN_MOS: Q2.1 (G), R8.1, U9.42 (PA2)
/FINN_SERVO_ONE: M1.1 (PWM), U9.26 (PD6)
/FINN_SERVO_TWO: M3.1 (PWM), U9.28 (PE0)
/GPS_MISO: U8.5 (TX), U9.22 (PD2)
/GPS_MOSI: U8.6 (RX), U9.23 (PD3)
/HOST_INTN: U2.14 (~H_INT~)
/LED_MOS: Q1.1 (G), R7.2, U9.20 (PD0)
/MCU_AVCC: C13.2, C15.2, FB1.2, U9.39 (AVCC)
/MCU_VCC: C11.1, C12.1, C14.1, C16.1, FB1.1, L1.2, U9.9 (VCC), U9.19 (VCC), U9.31 (VCC)
/MISO: MOD1.4 (DO8), U2.20 (H_SDA/MISO/TX), U5.6 (SDO), U9.16 (PC6)
/MOSI: MOD1.11 (AD4/DIO4), U2.17 (H_SA0/MOSI), U5.7 (SDI/SDA), U9.15 (PC5)
/OpenLog_GRN: U7.6 (GRN), U9.21 (PD1)
/OpenLog_MISO: U7.4 (TXO), U9.32 (PE2)
/OpenLog_MOSI: U7.5 (RXI), U9.33 (PE3)
/PA5-Hall_Effect: U6.3 (OUT), U9.1 (PA5)
/PA6-Therm: R1.2, TH1.1, U9.2 (PA6)
/PA7-Voltage: R3.1, R4.2, U9.3 (PA7)
/PDI_CLK: J1.5, R2.2, U9.35 (~RESET~/PDI_CLK)
/PDI_DATA: J1.1, U9.34 (PDI_DATA)
/RELEASE_MOS: Q3.1 (G), R9.1, U9.41 (PA1)
/Release_Servo: M2.1 (PWM), U9.29 (PE1)
/SCL: R10.2, U4.6 (SCL), U9.10 (PC0)
/SCLK: MOD1.18 (AD2/DIO2), U2.19 (H_SCL/SCLK/RX), U5.8 (SCLK), U9.17 (PC7)
/SDA: R11.2, U4.5 (SDA), U9.11 (PC1)
/~SS_5607: U5.4 (~CSB~), U5.5 (~CSB~), U9.14 (PC4)
/~SS_BNO080: U2.18 (~H_CS~), U9.13 (PC3)
/~SS_XBEE: MOD1.17 (AD3/DIO3), U9.12 (PC2)
GND: BT1.2 (-), C1.2, C2.2, C3.1, C4.2, C5.2, C6.1, C7.1, C8.1, C9.1, C10.2, C11.2, C12.2, C13.1, C14.2, C15.1, C16.2, D2.1 (K), D4.1 (K), J1.6, J2.4, J2.5, MOD1.10 (GND), Q1.2 (S), Q3.2 (S), Q4.2 (S), Q5.2 (S), R1.1, R4.1, U1.2 (GND), U2.2 (GND), U2.25 (GNDIO), U3.1 (GND), U4.4 (VSS), U5.2 (PS), U5.3 (GND), U6.2 (GND), U7.1 (BLK), U7.2 (GND), U8.7 (GND), U9.8 (GND), U9.18 (GND), U9.30 (GND), U9.38 (GND)
unnamed: C4.1, U2.9 (CAP)
unnamed: C6.2, R5.2, U4.8 (VDD)
unnamed: D1.1 (K), Q1.3 (D)
unnamed: D1.2 (A), R15.2
unnamed: D2.2 (A), R14.2
unnamed: D4.2 (A), R16.2
unnamed: D5.A, J2.1
unnamed: LS1.N, Q4.3 (D)
unnamed: M1.3 (-), M3.3 (-), Q2.3 (D)
unnamed: M2.3 (-), Q3.3 (D)
unnamed: Q5.3 (D), U1.3 (DATA)
unnamed: R6.2, U4.7 (~INT1~/CLKO)

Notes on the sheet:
Ports A & B have access to the ADC
Voltage Divider (6 —> 2)
MS5607 Pressure Sensor
Power Interface
Hall Effect Sensor
6V —> 3.3V Regulator
PDI Interface
BNO-080
Thermistor
Real Time Clock
XBEE

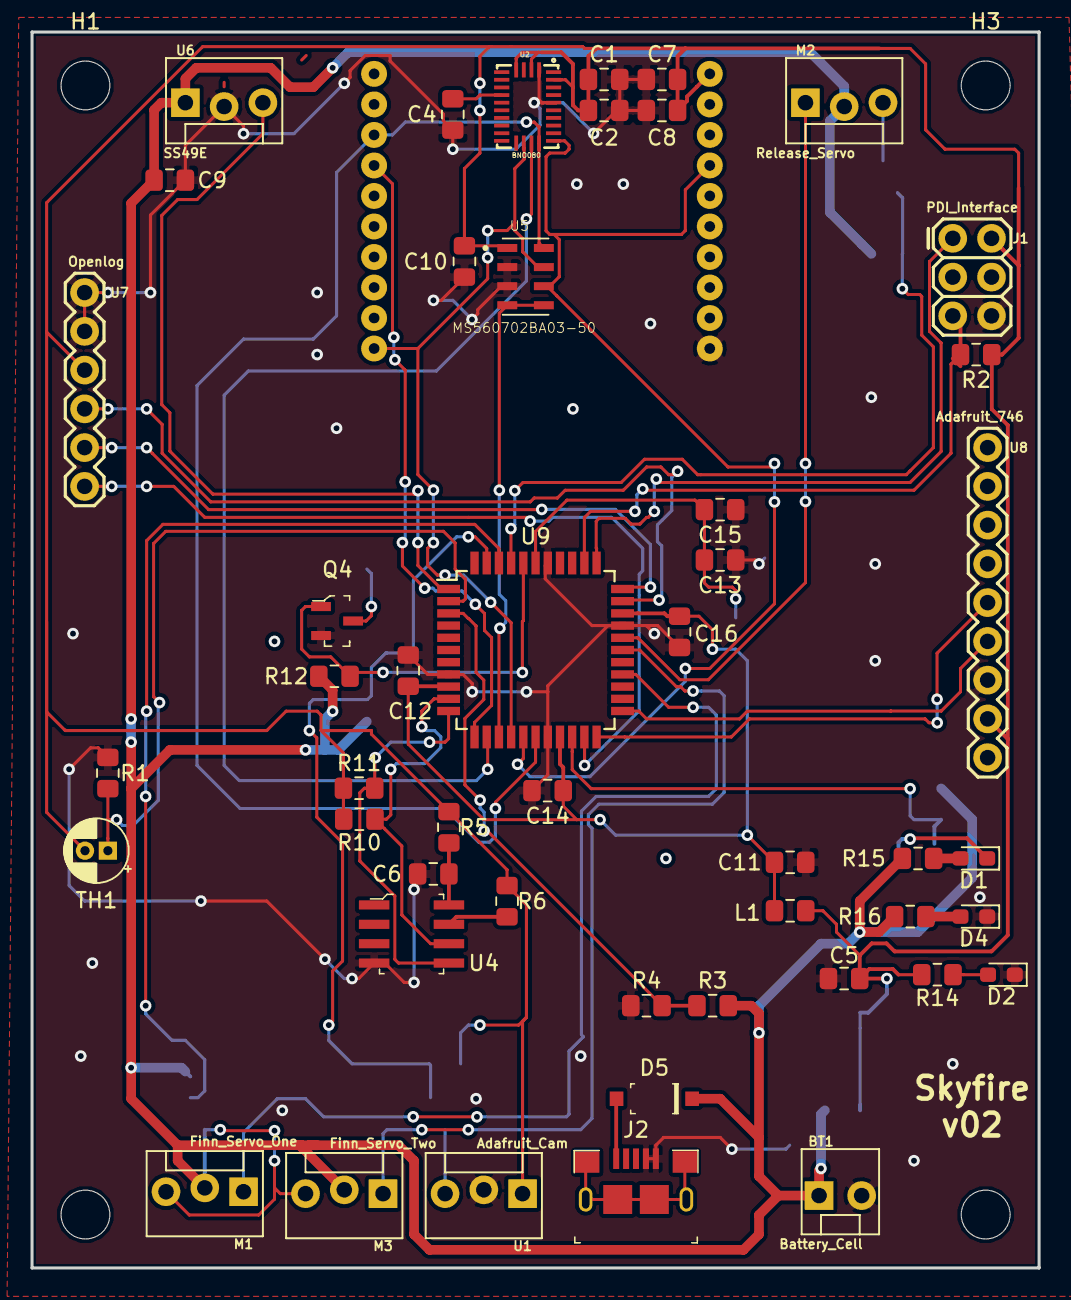
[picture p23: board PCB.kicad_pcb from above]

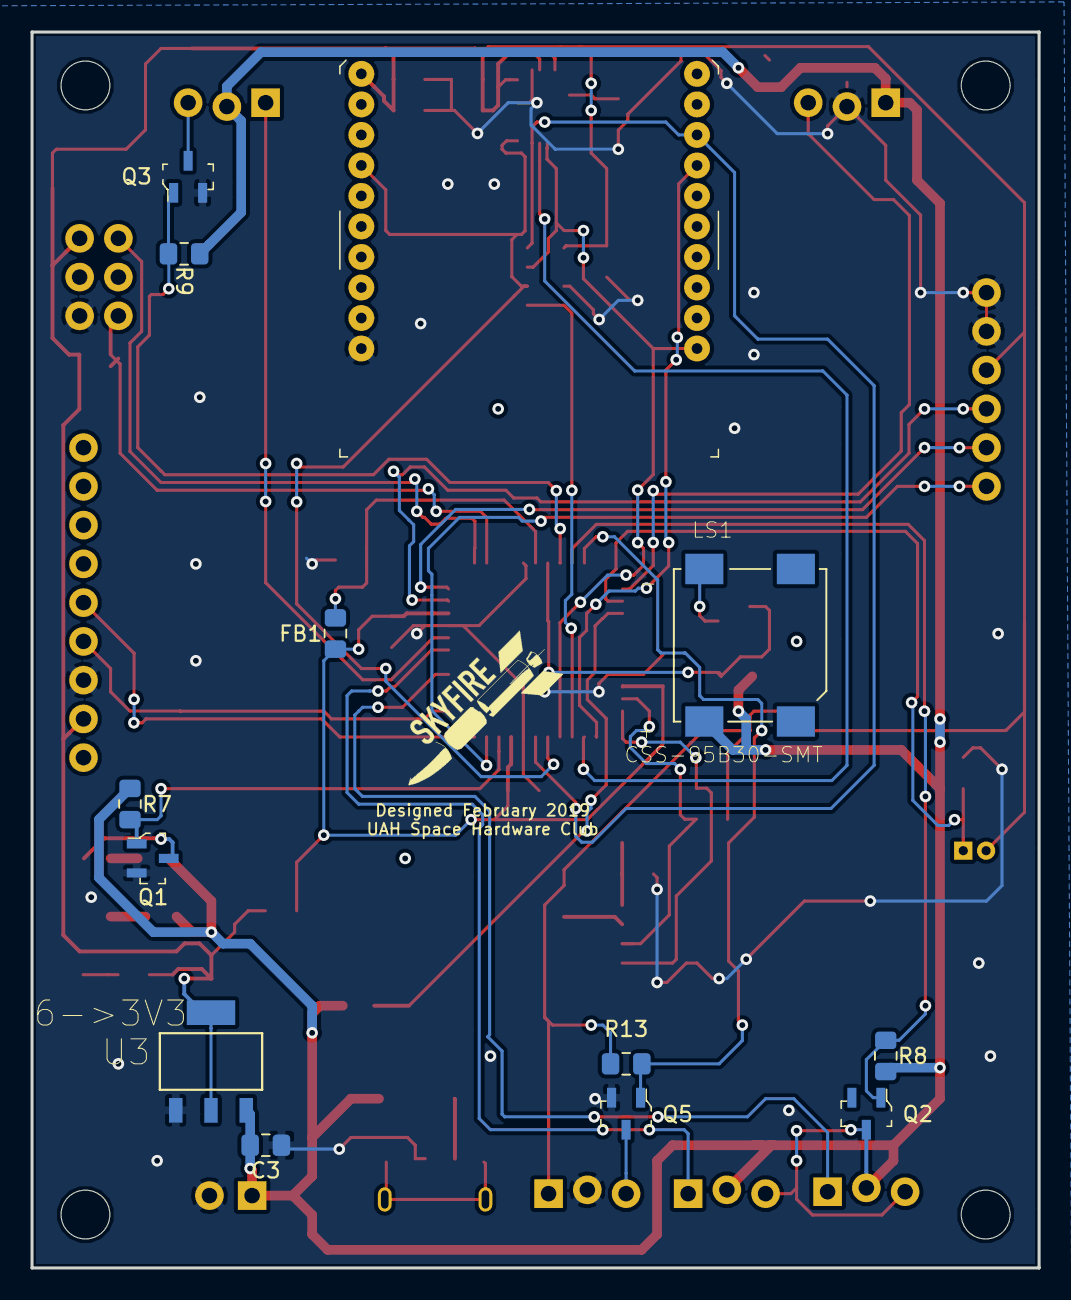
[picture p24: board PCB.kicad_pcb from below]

Board: 2 copper layers, 66.0 x 81.0 mm, 65 parts (13 on the bottom side), 43 nets.

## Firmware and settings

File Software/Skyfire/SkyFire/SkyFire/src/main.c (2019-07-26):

#include <asf.h>
#include <math.h>
#include <string.h>
#include "drivers\data_logger.h"
#include "drivers\thermistor.h"
#include "drivers\ms5607.h"
#include "drivers\mt3339.h"
#include "drivers\spi_controller.h"
#include "drivers\spy_cam.h"
#include "drivers\voltage.h"
#include "drivers\IMU.h"
#include "tools\RingBuffer.h"

// GCS Commands
#define RESET				'f'
#define CALIBRATE			'e'
#define CALIBRATE_ALTITUDE	'c'
#define CALIBRATE_ANGLE		'b'
#define SERVO_RELEASE		'a'
#define SERVO_CLOSE			's'
#define PACKET				'd'

// Tolerances for Flight State
#define EPSILON_VELOCITY	5
#define EPSILON_ALTITUDE	10

// Servo
#define SERVO_NEUTRAL_PULSE	750
#define SERVO_WAVELENGTH	10000
#define RELEASE_SERVO_OPEN	875
#define RELEASE_SERVO_CLOSE 600
#define SERVO_TRIM			-5

// EEPROM stuff
// uint16_t addr = PAGE | BYTE;
#define EEPROM_PAGE			0x1000	// Page 0
#define ALT_ADDR_BYTE0		0x00	// Byte 0
#define ALT_ADDR_BYTE1		0x01	// Byte 1
#define PACKET_ADDR_BYTE0	0x03	// Byte 3
#define PACKET_ADDR_BYTE1	0x04	// Byte 4
#define TIME_ADDR_BYTE0		0x06	// Byte 6
#define TIME_ADDR_BYTE1		0x07	// Byte 7
#define VEL_ADDR_BYTE0		0x1B	// Byte 27
#define VEL_ADDR_BYTE1		0x1C	// Byte 28
#define CHECK_WRITE_BYTE0	0x02	// Byte 2
#define CHECK_WRITE_BYTE1	0x1F	// Byte 31
#define STATE_BYTE			0x05	// Byte 5
#define RELEASED_BYTE		0x08	// Byte 8

// Ground Constants byte addresses
#define GROUND_PRESS_ADDR0  0x09	// Byte 9
#define GROUND_PRESS_ADDR1  0x0A	// Byte 10
#define GROUND_PRESS_ADDR2  0x0B	// Byte 11
#define GROUND_PRESS_ADDR3  0x0C	// Byte 12
#define GROUND_PRESS_ADDR4  0x0D	// Byte 13
#define GROUND_PRESS_ADDR5  0x0E	// Byte 14
#define GROUND_PRESS_ADDR6  0x0F	// Byte 15
#define GROUND_PRESS_ADDR7  0x10	// Byte 16
#define GROUND_TEMP_ADDR0	0x12	// Byte 18
#define GROUND_TEMP_ADDR1	0x13	// Byte 19
#define GROUND_TEMP_ADDR2	0x14	// Byte 20
#define GROUND_TEMP_ADDR3	0x15	// Byte 21
#define GROUND_TEMP_ADDR4	0x16	// Byte 22
#define GROUND_TEMP_ADDR5	0x17	// Byte 23
#define GROUND_TEMP_ADDR6	0x18	// Byte 24
#define GROUND_TEMP_ADDR7	0x19	// Byte 25

#define READ_EEPROM			0x06	// Load CMD, Load ADDR, Load CMDEX
#define ERASE_EEPROM		0x30	// Load CMD, Load CMDEX, Wait for BUSY flag to drop
#define	ERASE_PAGE_CMD		0x32	// Load CMD, Load ADDR, Load CMDEX, Wait for BUSY flag to drop
#define LOAD_BUFFER_CMD		0x33	// Load CMD, Load ADDR0, Load DATA0, Repeat 2-3
#define	WRITE_PAGE_CMD		0x34	// Load CMD, Load ADDR, Load CMDEX, Wait for BUSY flag to drop
#define	ATOMIC_WRITE_CMD	0x35	// Load CMD, Load ADDR, Load CMDEX, Wait for BUSY flag to drop
#define ERASE_BUFFER_CMD	0x36	// Load CMD, Load CMDEX, Wait for BUSY flag to drop
// BUSY flag is NVM.STATUS>>7

#define CTRLA_CMDEX_BYTE	0x01	// Tells NVM to execute the command
#define CCP_IOREG_MODE		0xD8	// Set CCP to this to allow CMDEX to be changed

///////////////////////// Function Prototypes //////////////////////////
void		system_init(void);												// Starts the system
void		pressure_init(void);											// Collects the sensors constants
void		gps_init(void);													// Starts the GPS
void		xbee_init(void);												// Starts the XBEE
void		bno_init(void);													// Starts the BNO055
void		hall_sensor_init(void);											// Starts the Hall Effect Sensor
void		change_hall_sensor_scaler(void);								// Updates the Hall Effect scale factor
void		release(void);													// Releases the Science Payload
double		get_pressure(void);												// Pascals
double		get_temperature(void);											// Celsius
double		get_altitude(double press);										// meters
double		get_voltage(void);												// Volts
double		diff(RingBuffer16_t* data, uint8_t frequency);					// Approximates velocity of CanSat
void		data_collect(RingBuffer16_t* alts, RingBuffer32_t* presses);	// Handles data collection
double		data_check(RingBuffer32_t* presses);							// Function that averages values and compares with stdev
void		imu_read(void);
void		pid_val(RingBuffer16_t* direct);								// Reads and calculates position of board
void		state_check(void);												// Returns the current state
void		release_servo_init(void);										// Starts Release Servo Rate
void		fin_servo_init(void);											// Starts PWM wave for fin servos
void		servo_pid(RingBuffer16_t* direct);								// Function that alters the position of the fins
void		clock_init(void);												// Starts a timer to count the seconds
void		time_update(void);												// Function to perform timer based actions
void		buzzer_init(void);												// Starts the buzzer
void		buzzer_stop(void);												// Stops the buzzer
void		calc_rpm(void);													// Function to calculate rpm for packets
void		update_scale_factor(void);										// Recalculates the scale factor of the hall effect based on input voltage
static void hall_sensor_measure(AC_t *ac, uint8_t channel, enum ac_status_t status); // Interrupt function for Hall Effect sensor

// XBEE controls
void	command(uint8_t c);												// Switch case for commands
void	reset(void);													// Re-initializes the CanSat
void	calibrate(void);												// Calibrates the payload (angle and altitude)
void	cali_alt(void);													// Calibrates the altitude
void	cali_ang(void);													// Calibrates the angle
void	servo_release(void);											// Opens the release servo (unlocks)
void	servo_close(void);												// Closes the release servo (locks)
void	packet(void);													// Transmits last packet stored

// EEPROM commands
void	eeprom_write_const(void);										// Writes the ground pressure and temp to EEPROM
void	eeprom_write(void);												// Writes the last packet to EEPROM
uint8_t	eeprom_read(uint16_t address);									// Reads the byte at specified address in EEPROM
void	eeprom_erase(void);												// Erases all bytes on all pages of EEPROM

/////////////////////////// Global Variables ///////////////////////////
volatile uint8_t state = 0;
volatile uint8_t released = 0;

double ground_p = 101325;		// Pascals standard sea level pressure
double ground_t = 288.15;		// 15 C

// Interrupt Flags
volatile uint8_t time_flag = 0;			// New data to write to EEPROM
volatile uint8_t xbee_flag = 0;			// New command received from ground station

// Hall Effect Constants
volatile uint8_t scale_factor = 0;		// updated with function

// Altitude calculation variables
double R = 287.0578987;
double L = -0.0065;
double g_0 = 9.80665;

// Pressure Calculation variables
uint16_t c[] = {0,0,0,0,0,0};

// XBEE
volatile uint8_t xbee_comm = 0; // Variable stores XBee commands

// IMU
volatile double ref_yaw = 180;				// Should be collected
volatile double ref_roll = 0;				// Ideal
volatile double ref_pitch = 90;				// Ideal

// RPM
volatile uint16_t ticks_per_sec = 0; // Hall effect interrupts per seconds (what a unit)

// GPS Stuff
char gps[15];						// GPS sentences
char dec[5];
volatile uint8_t writing = 0;
volatile uint8_t pos = 0;
volatile uint8_t word_pos = 0;
volatile uint8_t commas = 0;
volatile uint8_t idx = 0;

// EEPROM
volatile uint8_t check_write = 0; // Number used to verify successful write to EEPROM

// Output String
char str[100];

// Time and Packets
volatile uint16_t timer = 0;			// Time since startup
volatile uint16_t data_packets = 0;		// Number of times looped through data collection function
volatile uint16_t packets = 0;			// Number of packets since startup (equal to time at 1Hz transmission rate)
volatile uint16_t rate = 10;			// Frequency at which data is collected

// Initializes variables
volatile double press = 0;				// Pressure (Pa)
volatile double temp = 0;				// Temperature (C)
volatile double alt = 0;				// Altitude (m)
volatile double volt = 0;				// Battery Terminal Voltage (V)
volatile double velocity = 0;			// Velocity (m/s)
volatile double gps_t = 0;				// GPS Time
volatile double gps_lat = 0;			// GPS Latitude (+:N,-:S)
volatile double gps_long = 0;			// GPS Longitude (+:E,-:W)
volatile double gps_alt = 0;			// GPS Altitude
volatile int16_t gps_sats = 0;			// GPS Satellites
volatile double pitch = 0;				// Pitch Angle
volatile double roll = 0;				// Roll Angle
volatile double rpm = 0;				// Calculate RPM of Blades
volatile double angle = 0;				// Angle of Bonus Direction

// TEAM ID, TIME, PACKETS, ALTITUDE, PRESSURE, TEMPERATURE, VOLTAGE, GPS TIME, LATITUDE, LONGITUDE, GPS ALT, GPS SATS, PITCH, ROLL, BLADE SPIN RATE, FLIGHT STATE, BONUS DIRECTION
char* format = "5343,%u,%u,%i.%i,%li,%i.%i,%i.%i,%02i:%02i:%02i,%i.%li,%i.%li,%i.%i,%i,%i,%i,%i,%u,%i\n\0"; // Format for output string


////////////////////////////// Functions ///////////////////////////////
int main(void){
	system_init();
	delay_ms(100);

	// Turns on status LED
	PORTD.DIR |= PIN3_bm;
	PORTD.OUT |= PIN3_bm;
	buzzer_init();
	delay_ms(125);
	buzzer_stop();

	// Integer ring buffer for storing multiple older values
	int16_t alt_array[] = {0,0,0,0,0,0,0,0,0,0};
	RingBuffer16_t altitudes;	// in centimeters
	rb16_init(&altitudes, alt_array, (uint16_t) 10);

	int32_t press_array[] = {0,0,0,0,0,0,0,0,0,0};
	RingBuffer32_t pressures;	// in Pascals / 10
	rb32_init(&pressures, press_array, (uint16_t) 10);

	int16_t direct_array[] = {0,0,0,0,0,0,0,0,0,0};
	RingBuffer16_t directions;	// in hundredths degrees
	rb16_init(&directions, direct_array, (uint16_t) 10);

	// Boolean values of the state of the camera and buzzer
	uint8_t cam_initialized = 0;
	uint8_t buzzer_initialized = 0;

	// Camera switching
	int16_t cam_timer = -3;
	

	while(1){
		// Check Sensors
		data_collect(&altitudes,&pressures);

		// Checks the Flight State
		state_check();

		// IMU Check
		imu_read();

		if(timer - cam_timer == 2){
			cam_switch();
			cam_timer = -3;
		}
		//Gives each flight state their unique tasks
		switch(state){
			case 0:									// Flight State 0
				break;								// Do Nothing Special
			case 1:									// Flight State 1
				if(!cam_initialized){
					cam_initialized = 1;			// Ensures method is not called again
					cam_switch();					// Turns on Camera
					cam_timer = timer;				// Timer feature to ensure safe camera start
				}
				break;
			case 2:									// Flight State Two
				if(abs(alt-450)<EPSILON_ALTITUDE){	// Checks the altitude
					release();						// Releases the payload
					pid_val(&directions);			// Starts PID for Stabilization	
					ref_yaw = angle;				// Updates the reference yaw of the payload
				}
				else if(released){
					pid_val(&directions);	// Writes angle values to the ring buffer
					servo_pid(&directions); // Updates PID
				}
				if(!cam_initialized){
					cam_initialized = 1;
					cam_switch();
					cam_timer = timer;
				}
				break;
			case 3:
				if(!buzzer_initialized){
					buzzer_init();			//UNCOMMENT BEFORE FLIGHT
					buzzer_initialized = 1;
					
					cam_switch();
					cam_timer = timer;
				}
				break;
			default:
				state_check();
				break;
		}

		// 1 Hz timer interrupt function
		if(time_flag){
			temp = get_temperature();	// Grabs the temperature once
			volt = get_voltage();		// Updates voltage
			update_scale_factor();		// Updates Hall Effect scale factor
			calc_rpm();					// Resets the tick counter and averages it with the new values
			time_update();				// Transmits the data packet and writes the EEPROM
			time_flag = 0;
		}
		// XBEE command received
		if(xbee_flag){
			command(xbee_comm);
			xbee_comm = 0;
			xbee_flag = 0;
		}

		// Recalculates the data writing rate
		data_packets++;
		if(timer != 0){
			rate = data_packets / timer;
		}
	}
}


// Sensor functions
void system_init(void){
	// Initialization of systems
	sysclk_init(); // initializes the system clock
	delay_ms(2); // delays the rest of the processes to ensure a started clock
	sei();	// Enables global interrupts

	// Initialization of pins
	PORTC.DIR = 0xBC; // makes Port C have pins, 7, 5, 4, 3, and 2 be output (0b10111100)
	PMIC.CTRL = PMIC_LOLVLEN_bm | PMIC_MEDLVLEN_bm | PMIC_HILVLEN_bm; // enables all level interrupts

	// Driver Initialization
	cam_init();				// Initializes the Camera
	data_terminal_init();	// Initializes the OpenLog
	delay_ms(500);			// Delay to ensure clean writing
	xbee_init();			// Sets up XBEE command interrupt
	gps_init();				// Starts the GPS interrupt

	hall_sensor_init();		// Initializes the hall effect sensor (used here for debugging)
	thermistor_init();		// Initializes the thermistor
	voltage_init();			// Initializes the voltage reader
	spi_init();				// Initializes the SPI communication
	pressure_init();		// Initializes the pressure sensor
	bno_init();				// Initializes the IMU
	clock_init();			// Starts the clock for data transmission

	release_servo_init();	// Initializes the release servo
	fin_servo_init();		// Initializes the timer for the servo

	// Check EEPROM
	uint8_t b1 = eeprom_read(EEPROM_PAGE|CHECK_WRITE_BYTE0);
	uint8_t b2 = eeprom_read(EEPROM_PAGE|CHECK_WRITE_BYTE1);

	if((b1 == b2) && (b1 != 0xFF)){
		//printf("Reading EEPROM\n");
		uint64_t p =  ((uint64_t) eeprom_read(EEPROM_PAGE|GROUND_PRESS_ADDR7)<<56 | (uint64_t) eeprom_read(EEPROM_PAGE|GROUND_PRESS_ADDR6)<<48 |
					   (uint64_t) eeprom_read(EEPROM_PAGE|GROUND_PRESS_ADDR5)<<40 | (uint64_t) eeprom_read(EEPROM_PAGE|GROUND_PRESS_ADDR4)<<32 |
					   (uint64_t) eeprom_read(EEPROM_PAGE|GROUND_PRESS_ADDR3)<<24 | (uint64_t) eeprom_read(EEPROM_PAGE|GROUND_PRESS_ADDR2)<<16 |
					   (uint64_t) eeprom_read(EEPROM_PAGE|GROUND_PRESS_ADDR1)<<8  | (uint64_t) eeprom_read(EEPROM_PAGE|GROUND_PRESS_ADDR0));
		uint64_t t =  ((uint64_t) eeprom_read(EEPROM_PAGE|GROUND_TEMP_ADDR7)<<56  | (uint64_t) eeprom_read(EEPROM_PAGE|GROUND_TEMP_ADDR6)<<48 |
					   (uint64_t) eeprom_read(EEPROM_PAGE|GROUND_TEMP_ADDR5)<<40  | (uint64_t) eeprom_read(EEPROM_PAGE|GROUND_TEMP_ADDR4)<<32 |
					   (uint64_t) eeprom_read(EEPROM_PAGE|GROUND_TEMP_ADDR3)<<24  | (uint64_t) eeprom_read(EEPROM_PAGE|GROUND_TEMP_ADDR2)<<16 |
					   (uint64_t) eeprom_read(EEPROM_PAGE|GROUND_TEMP_ADDR1)<<8   | (uint64_t) eeprom_read(EEPROM_PAGE|GROUND_TEMP_ADDR0));
		memcpy(&ground_p, &p, 8);
		memcpy(&ground_t, &t, 8);

		alt = (double) ((int16_t) (eeprom_read(EEPROM_PAGE|ALT_ADDR_BYTE1)<<8 | eeprom_read(EEPROM_PAGE|ALT_ADDR_BYTE0)));
		timer = (uint16_t) (eeprom_read(EEPROM_PAGE|TIME_ADDR_BYTE1)<<8 | eeprom_read(EEPROM_PAGE|TIME_ADDR_BYTE0));
		packets = (uint16_t) (eeprom_read(EEPROM_PAGE|PACKET_ADDR_BYTE1)<<8 | eeprom_read(EEPROM_PAGE|PACKET_ADDR_BYTE0));
		state = eeprom_read(EEPROM_PAGE|STATE_BYTE);
		released = eeprom_read(EEPROM_PAGE|RELEASED_BYTE);
		//printf("Ground Pressure: %li\nGround Temperature: %i\n", (int32_t) ground_p, (int16_t) ground_t);
	}
	else{
		// Initialization of variables
		ground_p = get_pressure();
		ground_t = get_temperature();
		state = 0;
		eeprom_write_const();
	}
	
	temp = get_temperature();	// Grabs the temperature once
	volt = get_voltage();		// Updates voltage
	update_scale_factor();

	state_check();
}

void pressure_init(void){
	ms5607_init();

	// records the constants
	c[0] = ms5607_read(CMD_MS5607_READ_C1);
	c[1] = ms5607_read(CMD_MS5607_READ_C2);
	c[2] = ms5607_read(CMD_MS5607_READ_C3);
	c[3] = ms5607_read(CMD_MS5607_READ_C4);
	c[4] = ms5607_read(CMD_MS5607_READ_C5);
	c[5] = ms5607_read(CMD_MS5607_READ_C6);
	//printf("\n%u,%u,%u,%u,%u,%u\n",c[0],c[1],c[2],c[3],c[4],c[5]);
}

void gps_init(void){
	gps_uart_init();				// Starts the GPS
	delay_ms(2);

	(*GPS_TERMINAL_SERIAL).CTRLA = USART_RXCINTLVL_HI_gc;
}

void xbee_init(void){
	USARTE0.CTRLA = USART_RXCINTLVL_MED_gc;
}

void bno_init(void){
	sysclk_enable_module(SYSCLK_PORT_C, PR_TWI_bm);
	sysclk_enable_peripheral_clock(&TWIC);

	imu_init();

	imu_update();

	ref_roll = imu_roll();
	ref_pitch = imu_pitch();
	//ref_yaw = imu_heading();
}

struct ac_config aca_config;
void hall_sensor_init(void){
	memset(&aca_config, 0, sizeof(struct ac_config));

	ac_set_mode(&aca_config, AC_MODE_SINGLE);
	ac_set_hysteresis(&aca_config, AC_HYSMODE_LARGE_gc);
	ac_set_voltage_scaler(&aca_config, scale_factor);
	ac_set_negative_reference(&aca_config, AC_MUXNEG_SCALER_gc);
	ac_set_positive_reference(&aca_config, AC_MUXPOS_PIN5_gc);
	
	ACA.AC0CTRL |= AC_HSMODE_bm;

	ac_set_interrupt_callback(&ACA, hall_sensor_measure);
	ac_set_interrupt_mode(&aca_config, AC_INT_MODE_RISING_EDGE);
	ac_set_interrupt_level(&aca_config, AC_INT_LVL_MED);

	ac_write_config(&ACA, 0, &aca_config);

	ac_enable(&ACA, 0);

}

void change_hall_sensor_scaler(void){
	ACA.CTRLB = scale_factor;
}

void release(void){
	servo_release();
}

double get_pressure(void){
	double val = 101325;
	
	uint32_t d1 = ms5607_convert_d1();
	uint32_t d2 = ms5607_convert_d2();

	//printf("%lx, %lx\n", d1, d2);

	double dt = d2 - (uint64_t)c[4] * 256.0;
	//double temp = 20.0 + ((uint64_t) dt * c[5]) / 8388608.0;
	long double off = (uint64_t) c[1] * 131072.0 + ((uint64_t) c[3] * dt) / 64.0;
	long double sens = (uint64_t) c[0] * 65536.0 + ((uint64_t) c[2] * dt) / 128.0;

	val = (double) (((double) d1 * sens / 2097152.0 - off) / 32768.0);
	
	return val;	// returns pressure in Pa
}

// ADC linear fit constants
double m =  0.000494760310;
double b = -0.093185924650;

double get_temperature(void){
	double val = 298.15; // Change to 25 degrees C
	volatile uint16_t reading = thermistor_read();
	double voltage = (m * reading + b); // m and b are collected from testing
	double resistance = 3180.0 * (3.30 - voltage) / voltage; // 6720 is the resistance of the steady resistor
	val = (1.0 / (3.354016E-3 + 2.569850E-4 * log(resistance / 10000.0) + 2.620131E-6 * pow(log(resistance / 10000.0), 2) + 6.383091E-8 * pow(log(resistance / 10000.0), 3))); // returns the temperature in hundredths of kelvin
	return val; //returns the temperature in kelvin
}

double get_altitude(double press){
	double val = 0;
	val = ground_t * (pow(ground_p / press, R * L / g_0) - 1) / L;
	return (val);		//returns altitude in meters
}

double get_voltage(void){
	double reading = (double) voltage_read();
	double voltage = (m * reading + b); // m and b are collected from testing
	voltage = voltage * 29600.0 / 12540.0 + voltage; // 6720 is the resistance of the steady resistor
	return voltage;
}

// Approximates the Velocity from past five altitudes
uint8_t data_samples = 3;
double diff(RingBuffer16_t* data, uint8_t frequency){
	double val = 0;
	for(uint16_t i = 0; i < data_samples; i++){
		int32_t new = rb16_get_nth(data,i);
		int32_t old = rb16_get_nth(data,i+1);
		int32_t oldest = rb16_get_nth(data,i+2);
		val += ((3*new - 4*old + oldest) * frequency / 2.0); // O(h^2) approximation of backwards derivative (Thanks MAE284, you're good for something)
	}
	val /= data_samples;
	return (val/100);
}

void data_collect(RingBuffer16_t* alts, RingBuffer32_t* presses){
	//printf("In Data Collect\n");
	double p = get_pressure();
	int32_t p_i = (int32_t) (p * 10);
	rb32_write(presses,&p_i,1);
	double p_s = data_check(presses)/10.0;

	if(p_s != -1){
		press = p_s;					// Pulls middle value of pressures
		alt	= get_altitude(p_s);	// Uses the corrected pressure to calculate the altitude

		// Stores Altitude
		int16_t a = (int16_t) (alt*100);
		rb16_write(alts, &a, 1); // Writes altitude in buffer

		// Calculates Velocity
		velocity = diff(alts, rate);
	}
}

double data_check(RingBuffer32_t* presses){
	// Calculates average of data
	uint8_t length = 5;
	double mean = 0;
	for(uint8_t i = 0; i < length; i++){
		int32_t p = rb32_get_nth(presses, i);
		if(p > 700000 && p < 1100000){ // Checks to make certain value makes sense
			mean += ((double) p)/length;
		}
	}

	// Calculates standard deviation of data
	double stdev = 0;
	for(uint8_t i = 0; i < length; i++){
		int32_t p = rb32_get_nth(presses, i);
		if(p > 700000 && p < 1100000){
			stdev += pow(p-mean, 2);
		}
	}
	stdev /= (length - 1);

	// Throws out data that is farther than standard deviation from average
	double result = 0;
	uint8_t nums = 0;
	for(uint8_t i = 0; i < length; i++){
		int32_t p = rb32_get_nth(presses, i);
		if(p > 700000 && p < 1100000){
			if(abs(p - mean) <= stdev){
				result += p;
				nums++;
			}
		}
	}

	if(nums == 0){
		result = -1;
	}
	else{
		result /= (double) nums; // Averages the new values
	}
	return result;
}

void imu_read(void){
	imu_update();

	double r = imu_roll() - ref_roll;
	double p = imu_pitch() - ref_pitch;
	double y = imu_heading();

	if(abs(r) > 180){
		r = r - 360 * r / abs(r);
	}
	if(abs(p) > 90){
		p = p - 180 * p / abs(p);
	}
	if(abs(r) < 180 && abs(p) < 90){
		roll = r;
		pitch = p;
		angle = y;
	}
}

void pid_val(RingBuffer16_t* direct){
	double yaw = angle - ref_yaw;
	if(abs(yaw) > 180){
		yaw = yaw - 360 * yaw / abs(yaw);
	}
	int16_t y = (int16_t) (yaw *100); 
	rb16_write(direct,&y,1);
}

void state_check(void){
	switch(state){
		case 0:
			if((velocity < EPSILON_VELOCITY) && (alt > 450)){
				state++;
			}
			break;
		case 1:
			if(((velocity < EPSILON_VELOCITY) && (alt < 450)) || (released)){
				state++;
			}
			break;
		case 2:
			if((abs(velocity) < EPSILON_VELOCITY) && (alt < 25)){
				state++;
			}
			break;
		case 3:
			break;
		default:			
			if(released){							//This case is state = 2 and state = 3
				state = 2;
				if(alt < EPSILON_ALTITUDE){
					state = 3;
				}
			}
			else{									//This case is state = 0 and state = 1
				state = 0;
				if(velocity < EPSILON_VELOCITY){
					state = 1;
				}
			}
			
	}
}

void release_servo_init(void){
	sysclk_enable_peripheral_clock(&TCD0); //enables peripheral clock for TCD0
	sysclk_enable_module(SYSCLK_PORT_D, SYSCLK_HIRES); //necessary jumbo

	PORTD.DIR |= 0x07;
	TCD0.CTRLA = 0x05; // sets the clock's divisor to 64
	TCD0.CTRLB = 0x23; // enables CCA and Single Waveform
	TCD0.PER = SERVO_WAVELENGTH; // sets the period (or the TOP value) to the period
	TCD0.CCC = TCD0.PER - RELEASE_SERVO_CLOSE; // makes the waveform be created for a duty cycle // 514.5 ticks per millisecond
}

void fin_servo_init(void){
	PORTA.DIR |= PIN2_bm;
	PORTA.OUT |= PIN2_bm;
	
	TCD0.CTRLB |= 0x50;
	
	TCD0.CCA = TCD0.PER - (SERVO_NEUTRAL_PULSE + SERVO_TRIM);		// 400 is 90 degrees
	TCD0.CCB = TCD0.CCA;		// 750 is middle
}
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

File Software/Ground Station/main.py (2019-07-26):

import numpy as np
import pyqtgraph as pg
from pyqtgraph.Qt import QtGui, QtCore
from pyqtgraph import console
from pyqtgraph.dockarea import *
from realplot import RealTimePlot, update
import serial
import string

#  Open the serial port
ser = serial.Serial()
ser.timeout = 0.02
ser.baudrate = 115200
ser.port = 'COM9'
ser.open()

#comment

#  Commands
"""For use with the ground station to control the GUI"""
RESET = b'f'
CALIBRATE_PAYLOAD = b'e'
REQUEST_PACKET = b'd'
CALIBRATE_ALTITUDE = b'c'
CALIBRATE_ANGLE = b'b'
SERVO_RELEASE = b'a'
SERVO_CLOSE = b's'


#GUI Setup
app = QtGui.QApplication([])                    # Starts the GUI application
win = QtGui.QMainWindow()                       # Creates the main storage for docks
area = DockArea()                               # Creates an area to dock into
win.setCentralWidget(area)                      # Adds the area to the window space
win.resize(1400,800)                            # Sets the window size to 1400 pixels wide by 800 pixels tall
win.setWindowTitle("Skyfire Ground Station - Team 5343")    # Names the window

## Creates Docks and inserts them into the area
altituded  = Dock("Altitude")       # Check realplot.py for documentation
pressured  = Dock("Pressure")       # Creates plotting elements for each telemetry section
tempd      = Dock("Temp")
voltaged   = Dock("Voltage")
pitchd     = Dock("Pitch")
rolld      = Dock("Roll")
spind      = Dock("Blade Spin Rate")
directiond = Dock("Bonus Direction")
gpsd       = Dock("GPS")
messages   = Dock("Communication")
area.addDock(altituded, 'left')
area.addDock(pressured, 'bottom', altituded)
area.addDock(voltaged, 'bottom', pressured)
area.addDock(tempd, 'right', altituded)
area.addDock(gpsd, 'right', pressured)
area.addDock(pitchd, 'right', voltaged)
area.addDock(directiond, 'right', tempd)
area.addDock(spind, 'right', gpsd)
area.addDock(rolld, 'right', pitchd)
area.addDock(messages, 'right')

## Add Widgets to the docks
# Plots
wid = QtGui.QWidget()                           # Creates an empty Widget to hold a layout
lay = QtGui.QGridLayout()                       # Creates a layout to orgonaize the plots
wid.setLayout(lay)                              # Adds the layout to the container widget

altitude  = RealTimePlot(name="Altitude (m)")       # Check realplot.py for documentation
pressure  = RealTimePlot(name="Pressure (Pa)")       # Creates plotting elements for each telemetry section
temp      = RealTimePlot(name="Temp (°C)")
voltage   = RealTimePlot(name="Voltage (V)")
pitch     = RealTimePlot(name="Pitch (°)")
roll      = RealTimePlot(name="Roll (°)")
spin      = RealTimePlot(name="Blade Spin Rate (rpm)")
direction = RealTimePlot(name="Bonus Direction (°)")
gps       = RealTimePlot(name="GPS (°)")
altituded.addWidget(altitude.plot)          # Adds the widgets to the layout
pressured.addWidget(pressure.plot)
tempd.addWidget(temp.plot)
voltaged.addWidget(voltage.plot)
pitchd.addWidget(pitch.plot) 
rolld.addWidget(roll.plot)
gpsd.addWidget(gps.plot)
spind.addWidget(spin.plot)
directiond.addWidget(direction.plot)


# Buttons
w = QtGui.QWidget()                                                 # Creates a large widget to hold the others

halt_btn = QtGui.QPushButton('HALT')                                # A pushable button
calibrate_btn = QtGui.QPushButton('Calibrate Payload')
packet_btn = QtGui.QPushButton('Request Packet')
calibrate_altitude_btn = QtGui.QPushButton('Calibrate Altitude')
calibrate_angle_btn = QtGui.QPushButton('Calibrate Angle')
gps_btn = QtGui.QPushButton('GPS')
reset_btn = QtGui.QPushButton('RESET')
servo_release_btn = QtGui.QPushButton('Servo Release')
servo_close_btn = QtGui.QPushButton('Servo Close')

halt_btn.setCheckable(True)                          # Allows for a button to stay pressed
calibrate_btn.setCheckable(True)
packet_btn.setCheckable(True)
calibrate_altitude_btn.setCheckable(True)
calibrate_angle_btn.setCheckable(True)
gps_btn.setCheckable(True)
reset_btn.setCheckable(True)
servo_release_btn.setCheckable(True)
servo_close_btn.setCheckable(True)

listw = QtGui.QListWidget()                     # Creates a display list box
cmdw = QtGui.QLineEdit()                        # Creates a line editor
mission_timew = QtGui.QLabel()                  # Creates a text label
packetsw = QtGui.QLabel()
flight_statew = QtGui.QLabel()
gps_timew = QtGui.QLabel()
gps_altw = QtGui.QLabel()
gps_satsw = QtGui.QLabel()

mission_timew.setText('<b>Mission Time (s):</b>')       # Set the initial text of the labels to the data they reperesent
packetsw.setText('<b>Packets:</b>')
flight_statew.setText('<b>Flight State:</b>')
gps_timew.setText('<b>GPS Time (UTC):</b>')
gps_altw.setText('<b>GPS Altitude (m):</b>')
gps_satsw.setText('<b>GPS Sats:</b>')

layout2 = QtGui.QGridLayout()                   # Creates a layout element
w.setLayout(layout2)                            # Adds the layout to the large widget
messages.addWidget(w)                           # Adds the large widget to the dock

layout2.addWidget(reset_btn,                7, 0, 1, 2)     # Widget goes in row 7, column 0, spanning 1 row and 2 columns
layout2.addWidget(halt_btn,                 8, 0, 1, 1)
layout2.addWidget(listw,                    0, 0, 1, 2)
layout2.addWidget(cmdw,                     1, 0, 1, 2)
layout2.addWidget(packet_btn,               9, 0, 1, 1)
layout2.addWidget(calibrate_altitude_btn,   9, 1, 1, 1)
layout2.addWidget(calibrate_angle_btn,      8, 1, 1, 1)
layout2.addWidget(calibrate_btn,            10, 1, 1, 1)
layout2.addWidget(gps_btn,                  10, 0, 1, 1)
layout2.addWidget(servo_release_btn,        11, 0, 1, 1)
layout2.addWidget(servo_close_btn,          11, 1, 1, 1)
layout2.addWidget(mission_timew,            3, 0, 1, 1)
layout2.addWidget(packetsw,                 4, 0, 1, 1)
layout2.addWidget(flight_statew,            5, 0, 1, 1)
layout2.addWidget(gps_timew,                3, 1, 1, 1)
layout2.addWidget(gps_altw,                 4, 1, 1, 1)
layout2.addWidget(gps_satsw,                5, 1, 1, 1)

# Show Window
win.show()
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

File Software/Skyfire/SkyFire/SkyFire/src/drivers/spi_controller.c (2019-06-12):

/*
 * spi_controller.c
 *
 * Created: 9/3/2018 12:50:35 PM
 *  Author: cellis
 */ 

#include <asf.h>
#include "spi_controller.h"

void spi_init(void)
{
	PORTC.DIR |= 0b10110000; 
	sysclk_enable_peripheral_clock(&SPIC);
	SPIC.CTRL = 0x50; //enables SPI and puts a prescaler of 16 idling high and transmitting MSB first on rising signal
}

void spi_select(uint8_t port)
{
	PORTC.OUT ^= port; //switches SS
}

volatile uint8_t spi_read(void)
{
	uint8_t oldInterruptState = SREG;
	cli();
	SPIC.DATA = 0xFF; // make the DATA register something we know
	while(!(SPIC.STATUS>>7));
	sei();
	SREG=oldInterruptState;
	return SPIC.DATA; // return the data from this function
}

void spi_write(uint8_t data)
{
	uint8_t oldInterruptState = SREG;
	cli();
	SPIC.DATA = data; // write the data we want to send to the data register
	while(!(SPIC.STATUS>>7)); // wait to ensure the data is sent before we do anything else
	sei();
	SREG=oldInterruptState;
}

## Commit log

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2018-12-15 Implement power circuit
    [PCB.sch]
2018-12-15 Fixed little bug
    [PCB.sch]
2018-12-15 Added PDI interface for MCU (maybe)
    [PCB.sch]
2018-12-15 Start implementing MS5607 application circuit
    [PCB.sch]
2018-12-15 Implement AP3419 appliation circuit
    [PCB.sch]
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2018-12-18 Grounded the xmega
    [PCB.sch]
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2019-01-03 Just a bunch of .dat and .pts files
    [6409_points.csv]
2019-01-03 GUI update
    Improved the layout of the GUI to be closer to the final product. Forgive the comments, or lack, but it was just a repetition of old work.
    [Flight_5343.csv]
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2019-01-03 Added SS490 Hall effect symbol
    [PCB.sch]
2019-01-06 Revert "Merge branch 'master' of https://github.com/arspauld/CanSat"
    This reverts commit bc53826c9e0eb044944db2bb0ee00b51452b93e5, reversing
    changes made to 81d7122374d882940c6ee23d8daad00bd2ded12f.
    [Flight_0115.csv]
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2019-01-23 Trashed dsgn models+ dual rotor export
    [2018-cssf-300_asm.stp]
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2019-01-23 Revert "fasjgfkjFH"
    This reverts commit b96720fae449464ffa4fcaa81186aff08d1970dc.
    [CANSAT_CHASSIS.cfg]
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2019-01-23 Ditched design into step final
    [2018-cssf-000_asm.stp]
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2019-01-23 Naca blade modeled in step!
    [6409_blade.step, bigsketch.dxf, smallsketch.dxf]
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2019-01-23 Container Done - kinch
    [Container Assembly.cfg]
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2019-01-26 the Springs are janky
    [Container Assembly.cfg]
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2019-01-27 Final push for tonight??
    [Container Assembly.cfg, Lip1.psm]
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2019-01-30 Matlab is kicking my ass
    [Cd_vs_Alpha_data.csv, Cl_vs_Alpha_data.csv, coefs.xlsx]
2019-01-31 Create Container 2 parts.iges
    [Container 2 parts.iges]
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2019-02-01 Container 2 shell constraints
    [Container 2 asm.cfg, OLD_ASM.cfg]
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2019-02-06 Wing X section stls made
    [20cm_0012_rotor_xsect_1.stl, 20cm_0012_rotor_xsect_2.stl, 20cm_0012_rotor_xsect_3.stl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]
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2019-02-07 Add a lot of libraries and footprints
    [PCB.sch]
2019-02-07 Generated initial PCB from schematic
    [PCB.kicad_pcb, PCB.sch]
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2019-02-08 Fix Batteries
    [PCB.kicad_pcb, PCB.sch]
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2019-02-08 Fix Connector
    [PCB.kicad_pcb, PCB.sch]
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2019-02-08 I think its done, but holy shit its bad
    [PCB.kicad_pcb]
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2019-02-12 second rotor set stls
    [20cm_0012_rotor_xsect_1_mirror.stl, 20cm_0012_rotor_xsect_2_mirror.stl, 20cm_0012_rotor_xsect_3_mirror.stl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]
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2019-02-12 fix the libraries
    [PCB.kicad_pcb, PCB.sch]
2019-02-13 Layout and edge cuts
    [PCB.kicad_pcb]
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2019-02-15 fix logo
    [PCB.kicad_pcb]
2019-02-15 fix silk screen
    [PCB.kicad_pcb]
2019-02-26 added stl for whole rotor
    [20cm_0012_rotor.stl, Container Assembly.cfg]
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2019-03-07 getting more parts for printing
    [2018-CSSF-303_TOP.stl, Container Assembly.cfg]
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2019-03-27 gaaah dang this gonna be a lot
    [Container Assembly.cfg]
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2019-04-04 didn't fully save my last one
    [Container Assembly.cfg]
2019-04-05 ROTOR_HUB_V2 created
    It's essentially the same part as before, with the same dimensions and such. No dowel holes, but otherwise functionally the same, just modeled in Solid Edge.
    [Container Assembly.cfg]
2019-04-06 Added stops in line with the cansat axis on the top blades(partially), and stops on the new(and old) rotor hubs.
    computer ran out of battery, so rotor adapters still need to be smoothed out and have the holes redone
    [Container Assembly.cfg]
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2019-04-07 fun things
    - created csv_creation.py
    - started adding commands to main.py
    - edited realplot.update to include the app in the function arguments
    [Flight_0115.csv, Flight_5343.csv]
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2019-04-12 code and drop test stuff
    [drop data video analysis.xlsx]
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2019-04-19 V2 hub adapter stl added
    [hub_adapter v1.stl]
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2019-05-13 timer fix
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2019-05-16 stl files added
    stl files
    [PCB_CASE_V3_BACK.stl, PCB_CASE_V3_FRONT.stl, U-Frame ASSM.cfg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]
2019-05-16 Update Container Top V3 (Dimensions too large).par
    parachute bolt holes added
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2019-05-17 added SD card protector piece
    [U-Frame ASSM.cfg]
2019-05-17 Finished up ground station, cleaned up folder
    [Flight_0115.csv, Flight_5343.csv]
2019-05-19 code shit
    gps now works and xbee is on spi, but doesn't work
    [main.c, ms5607.c, mt3339.h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]
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2019-05-20 CLEANING UP STUFF
    CAPSLOCK IS ON. OOPS
    [BIGGER_MICRO_SERVO_ASM.cfg, CONTAINER_ASSEM.cfg, U-Frame ASSM.cfg]
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2019-05-28 ROTOR LOCKS
    Might use these to keep rotors from folding up when landing
    [TOP_ROTOR.cfg, U-Frame ASSM.cfg]
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2019-06-02 fixed data overload on GCS
    [main.c]
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2019-06-02 confirmation using OneMonth board approved code
    [Flight_5343 (test flight).csv, Flight_5343.csv]
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2019-06-04 Blade Redesign
    X-Cross Bars
    [20cm_0012_rotor_cutouts.stl, 20cm_0012_rotor_cutouts_mir.stl, 3_ROTOR_ASSEM.cfg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]
2019-06-05 New hubs for Sign Board/ Redesign of Back PCB Case
    [Container Top V4.stl, PCB_CASE_V3_BACK.stl, hub_adapter_signboard v1.stl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]
2019-06-05 Code updates
    will test BNO
    [Flight_5343.csv]
2019-06-06 Magnet rotor hole, signboard adapter correct dimensions
    [ROTOR_HUB_V2_bottom.stl, hub_adapter_signboard v2.stl]
2019-06-06 Worked on Servos and buzzer
    [data_logger.h, main.c]
2019-06-06 PCB cases updated for 2 servo design
    [RELEASE_ARM.stl, ROTOR_HUB_V2_bottom.stl, U-Frame_assem V2.cfg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]
2019-06-06 updates to pcb_case v4 and assem v2
    [U-Frame_assem V2.cfg]
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2019-06-06 fin design partway done, increased magnet hole size to 7mm
    [ROTOR_HUB_V2_bottom.stl, U-Frame ASSM.cfg, U-Frame_assem V2.cfg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]
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2019-06-06 DRONE MOTORS ARE BACK
    [U-Frame ASSM.cfg]
2019-06-07 updates tp signboard adapters
    [hub_adapter_signboard v1.stl, hub_adapter_signboard v1_mir.stl]
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2019-06-09 FILES JUMBLED TEST-- PUSHING FROM ZAC'S OLD LAPTOP
    Files that will need updating:
    ROTOR_HUB_V2_bottom
    Files that MiGhT need updating:
    everything???
    [CONTAINER_ASSEM.cfg, Container Top V4.stl, FinR_V2.stl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]
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2019-06-10 flight state logic fixed
    [main.c]
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2019-06-10 Fixed the pressure sensor
    [main.c, ms5607.c, spi_controller.c]
2019-06-10 file updates/recovery, renaming continued. No new/modified files as far as I know
    [FinR_V2.stl, FinR_connector_V1.stl, PCB_CASE_V5_BACK.stl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]
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2019-06-10 flight state logic reworked
    [main.c, main.py]
2019-06-11 frequency for buzzer changed
    [main.c]
2019-06-11 PWM was flipped
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2019-06-11 cleaned up main.py, edited README
    [Flight_5343.csv]
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2019-06-12 im a big dumb so i fixed the adc
    rip
    [main.c, voltage.c]
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2019-06-12 fixed calibrate commands in GUI
    [Flight_5343.csv]
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2019-06-12 moved around conditionals and new flight data
    [Flight_5343.csv]
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2019-06-13 flight calculations and slight edits
    [Flight_5343 (another test flight again again).csv, Flight_5343 (another test flight again).csv, Flight_5343 (last flight of the day).csv]
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2019-06-15 container top stl updated
    [Container Top V4.stl]
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2019-06-16 cansat final flight data
    [Flight_5343 (real flight).csv, Flight_5343.csv]
